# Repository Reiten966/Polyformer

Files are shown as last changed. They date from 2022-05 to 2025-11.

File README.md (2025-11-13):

# Polyformer
## To Reshape, Recreate, Reproduce.

As of late 2025, Polyformer is *no longer supported* due to a shift of focus in my life. Thanks for the amazing support of the community over the past 3 years. You could follow my future work at @reiten966

Polyformer is an open-source project that aims to recycle plastics into FDM filaments

Join the [Discord](https://discord.gg/jUtHzhddZZ) for Q&A. Please consider signing up for Patreon or Github sponsorship, link is on the right.

Note: The EBB42 V1.2.1 in the kit is no longer conpatible with the old firmware, please source EBB42 V1.2/V1.1 or help updating the firmware to support the new board.

The part kit is available at [Triangle Lab-Global](https://s.click.aliexpress.com/e/_DFp1dtz) and [DFH-US](https://dfh.fm/collections/new-products/products/polyformer-kit-by-reiten966).

Make sure your printer can print over 260C and is not PTFE lined.

Working on this project will expose you to HIGH VOLTAGE COMPONENTS and moderate amount of VOC. Please ask for help from a maker or electrician with the electronics assembly. The project owner is not responsible for any damage and loss to the end users.

Hero_34

Opening_Animation

[Project Page](http://www.reiten.design/polyformer)

[OSHWA US002136](https://certification.oshwa.org/us002136.html)

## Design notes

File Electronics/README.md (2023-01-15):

# Firmware Setup

If you bought the PF kit or plan to use EBB42 and Alexware, please refer to the EBB42 + Alexware folder.

If you plan to use klipper, please refer to the klipper folder.

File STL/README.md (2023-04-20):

# Print Guide

- The parts are DESIGNED to be manufactured with FDM technology with the proper tolerance stack in mind.

- Material Usage as of (9/21/2022): 1255g (2000g with panels) Main color and 400g accent color (1.25g/mm3 density). (We are constantly working on reducing the usage)

- Before you print anything, please print the [**PolyCube**](https://github.com/Reiten966/Polyformer/blob/main/STL/PolyTools) under the Tools folder and post your result in #print_help. The cube is a test for evaluating printer's performance and accuracy, we will help you intepret the result and suggest ways you can improve the quality.

- Use [**PolyTray**](https://github.com/Reiten966/Polyformer/blob/main/STL/PolyTools/PolyTray.STL) to organize your bolts and screws while building the Polyformer.

- Always dry your filament before printing mechanical parts, especially PETG. The blobs and strings cause by wet filaments can cause binding and malfunctioning the gearbox.

- The parts should be printed with at least **4 perimeters, 6 top and bottom layers**, set the seam type to "aligned" in Superslicer, or set to "sharpest corner" and "smart hiding" in Cura, **20% infill and 0.2mm layer height**. Cubic or gyro infill are usually pretty good. If you are using clear filament, Grid and honeycomb infill looks the nicest. You can also do concentric fill for your top and bottom layers which will look very nice.

- If you run into fitment issues and your printer has already been calibrated, try changing the "horizontal expansion" to -0.05 and increase if needed.

- Please also adjust the expansion rate in the slicer, you can do so by scaling the model only in XY direction by percentage, ABS has about ~0.6% shrinkage, PETG has about ~0.15%, I am not too sure about PLA (it has a lesser tendency to shrink than PETG so probably negligible) but you can do a test by printing a long bar across the plate and measure the dimension to calculate the shrinkage.

- In regards to the temperature for heatset inserts, PLA is around 225 °C, PETG is 245 °C, and ABS is 265 °C.

- All the functional parts can be printed on a 200mm x 200mm build plate. The panels can be printed on a 220mm x 200mm plate.

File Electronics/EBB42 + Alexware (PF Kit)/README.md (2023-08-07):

# Firmware for the PolyFormer stand alone pulling system
---

## Wiring Diagram
### EBB42
Wiring_Diagram_EBB42

### EBB36
Wiring_Diagram_EBB36

* [Wiring Guide In-Progress](https://discord.com/channels/969539629176991764/1062541608559579187)
* [Firmware deployment guide](firmware_deployment_guide.md)

Permission is hereby granted, free of charge, to any person obtaining a copy of this software and associated documentation files (the "Software"), to deal in the Software without restriction, including without limitation the rights to use, copy, modify, merge, publish, distribute, sublicense, and/or sell copies of the Software, and to permit persons to whom the Software is furnished to do so, subject to the following conditions:

The above copyright notice and this permission notice shall be included in all copies or substantial portions of the Software.

THE SOFTWARE IS PROVIDED "AS IS", WITHOUT WARRANTY OF ANY KIND, EXPRESS OR IMPLIED, INCLUDING BUT NOT LIMITED TO THE WARRANTIES OF MERCHANTABILITY, FITNESS FOR A PARTICULAR PURPOSE AND NONINFRINGEMENT. IN NO EVENT SHALL THE AUTHORS OR COPYRIGHT HOLDERS BE LIABLE FOR ANY CLAIM, DAMAGES OR OTHER LIABILITY, WHETHER IN AN ACTION OF CONTRACT, TORT OR OTHERWISE, ARISING FROM, OUT OF OR IN CONNECTION WITH THE SOFTWARE OR THE USE OR OTHER DEALINGS IN THE SOFTWARE.

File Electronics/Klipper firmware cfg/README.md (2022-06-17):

printer.cfg is for option 1

polyformer.cfg is for option 2

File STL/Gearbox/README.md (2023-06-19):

60% more torque at 2/3 the efficiency of the original!

Print two of each of the planet gears. When assembling, the planet gears should be evenly spaced around the ring gear (ie 90 degrees apart) and matching planets should be opposite each other. The faces with the squares/circles should be facing up (ie away from the stepper motor).

Print in PLA/PLA+ using the recommended PF print settings. I haven't tested this design with other materials but I'd avoid PETG as it flexes too much and will likely cause binding. If you print it out of something other than PLA/PLA+ I'd be interested to know how you go!

Tolerances are mostly baked into the design.

Heat set inserts go into the 4 holes in the output gear and these line up with the holes in the spool holder.

Link to Onshape document: https://cad.onshape.com/documents/80025b16f3dc0090e209a16d/w/86596204eff784e693332d0d/e/ddea801f1fdb4b026ff6d2b4 There's a bunch of other nonsense in there as well. I don't guarantee that any of it will work.





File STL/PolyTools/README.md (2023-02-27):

# PolyTools

## PolyCube

Testing printer accuracy and overhang capability

Items that are tested:

-45 degree overhangs

-Print-in-place tolerance

-Flow percentage

-Compliant 12mm tube fastener

-Bearing fitment

-Vertical 12mm tube fitment

Post your result in #print_help

How to read Polycube

## PolyPlane

Used for sharpening bearings, achieving a better cutting performance

-4x M3x8mm

-6x 623 bearings

## PolyTray

Identifying screws size and storing screws

-19x 6x3mm Neodymium magnets

## PolyClip

Constructing bigger boxes using smaller boxes for bottle collection

-No assembly, print-in-place

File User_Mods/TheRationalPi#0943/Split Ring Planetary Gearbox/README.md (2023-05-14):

THIS IS NOW THE OFFICIAL GEARBOX AND PROBABLY WON'T BE UPDATED HERE, JUST GET IT FROM THE STL FOLDER

60% more torque at 2/3 the efficiency!

This is my 70:1 split ring planetary gearbox for the PolyFormer. It uses the existing gearbox as a base and should be a drop-in replacement. This uses the existing gearbox cap, grab that from the main STL/Gearbox folder. Print two of each of the planet gears. When assembling, the planet gears should be evenly spaced around the ring gear (ie 90 degrees apart) and matching planets should be opposite each other. The faces with the squares/circles should be facing up (ie away from the stepper motor).

Print in PLA/PLA+ using the recommended PF print settings. I haven't tested this design with other materials but I'd avoid PETG as it flexes too much and will likely cause binding. If you print it out of something other than PLA/PLA+ I'd be interested to know how you go!

Tolerances are mostly baked into the design.

Heat set inserts go into the 4 holes in the output gear and these line up with the holes in the spool holder. These are the same M3 x 5 x 4 heat set inserts as used in the PF BOM. 

Link to Onshape document: https://cad.onshape.com/documents/80025b16f3dc0090e209a16d/w/86596204eff784e693332d0d/e/ddea801f1fdb4b026ff6d2b4

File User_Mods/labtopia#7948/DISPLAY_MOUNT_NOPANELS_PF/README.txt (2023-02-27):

labtopia#7948
2_19_23
LABTOPIAS_IMPERFECT_DFHKIT_DISPLAY_MOUNT

I made this quickly to mount the DFH kit display for my polyformer with no panels.  It slides into the holes of the frame.  I drilled pilot holes into the screw mount points and used some short small screws.
.stl only

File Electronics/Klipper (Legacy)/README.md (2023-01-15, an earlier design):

# Firmware Setup

### Its a good idea to flash the firmware for Pi and MCU **BEFORE** you follow the part 4 video to install them on the machine.

## Option2: (Klipper: Voron printer + Compatible MCU)

- Plug the SKR pico to the pi via USB on your printer, and add the polyformer.cfg into your printer's config as below
  
- And then include the polyformer.cfg in your main printer.cfg as below
  

- Follow the Klipper installation on SKR Pico above.

## Option3: (Marlin: Compatible MCU + Screen)

Guide in progress, please ask in the discord.

# Wiring Guide

- UART setup
  Polyformer-Electronics-RPi-SKR-Pico1 0

- USB setup
  

# PID Calibration Procedure

This procedure is for calibrating the heater cartridge.

**Reference documentation**

- [Bigtree SKR Pico v1.0 + RPi setup](https://3dwork.io/en/skr-pico-analysis-and-complete-guide-of-this-great-little-controller)
- [Basic Klipper Configuration](https://3dwork.io/en/skr-pico-analysis-and-complete-guide-of-this-great-little-controller/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)
- [Mainsail](https://docs.mainsail.xyz/)
- [Installing MainsailOS](https://docs.mainsail.xyz/setup/mainsail-os)
- [Klipper3D](https://www.klipper3d.org)

## Pre-reqs

The following instructions assume the following:

- Your hardware setup matches the diagram the provided diagram `Polyformer-Electronics-RPi-SKR-Pico1.0-Working.png`
- Your RaspberryPi has been configured for UART integration. If not, follow this guide [Basic Klipper Configuration](https://3dwork.io/en/skr-pico-analysis-and-complete-guide-of-this-great-little-controller/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)
- _MainsailOS_ (_Mainsail_, _klipper_, and _Moonracker_) are install and running on the _RaspberryPi_
- Your _SKR Pico v1.0_ control board has been flashed with the latest stable firmware and has `UART` support. The name of your firware image should be `klipper-UART0.uf2`
- You are using the attached klipper config `printer.cfg`
- _Mainsail_ web UI is acceesible and there are no errors reported by klipper on the _Mainsail_ dashboard.

**IMPORTANT:** ALL pre-qeqs MUST be satified in order to proceed.

## Instructions

1. Open a web brower and go to the Mainsail website that is running on your RapsberryPi
2. Open the _G-Code console_ on the Mainsail web UI
3. Run the following g-code command to calibrate. This will take about 5 minutes to complete:

```
PID_CALIBRATE HEATER=extruder TARGET=210
```

4. Run this command to save the PID calibration coeffs to the 'printer.cfg' file

```
SAVE_CONFIG
```

5. Click the _Save and Restart_ button to reconfigure _Klipper_
6. Verify temperature stabiity

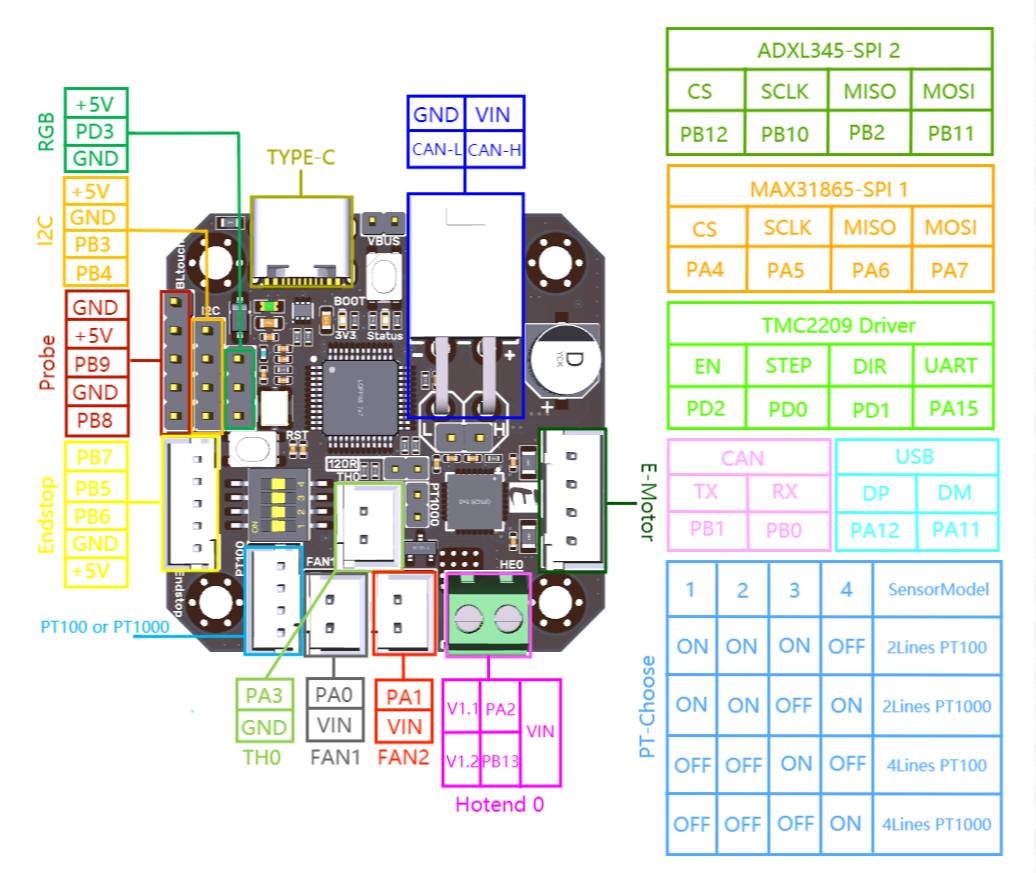
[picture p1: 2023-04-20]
Electronics/EBB42 + Alexware (PF Kit)/images/EBB42 CAN V1.1&V1.2-PIN.png

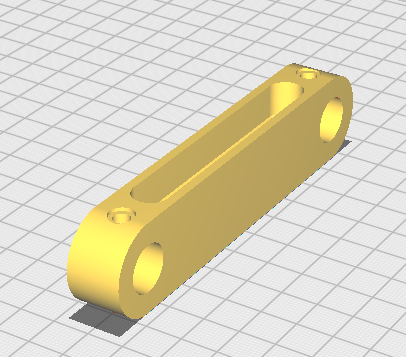
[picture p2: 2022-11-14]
STL/Carriages/Images/Electronics_Bracket_4x.png

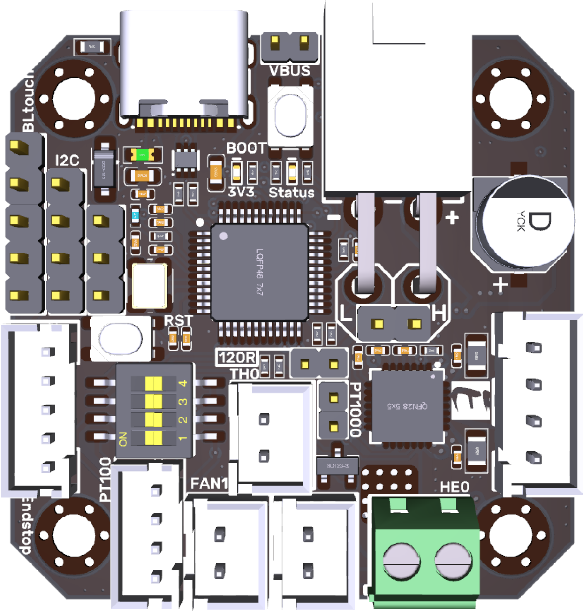
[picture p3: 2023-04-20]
Electronics/EBB42 + Alexware (PF Kit)/images/EBB42 CAN V1.1&V1.2.png

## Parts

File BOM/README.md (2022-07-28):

[BOM](https://docs.google.com/spreadsheets/d/1AnlkvCJu0GFPeh3ZkoAeYPVGYUqE0VFktIv_mGqOwsU/edit#gid=570414797)

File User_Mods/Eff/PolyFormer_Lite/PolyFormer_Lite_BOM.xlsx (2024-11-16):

Category | Part | Qty | Price/Un (BRL) | Total Price(BRL) | Price (direct USD conversion)
Electronics | Knock-off E3D V6 HotEnd Assembly | 1 | R$99.00 | R$99.00 | $16.89
 | W1209k Thermostat Board | 1 | R$39.00 | R$39.00 | $6.66
 | PWM controller | 1 | R$40.00 | R$40.00 | $6.83
 | Jgy370 12v Dc Motor | 1 | R$90.00 | R$90.00 | $15.36
 | 60x10 PC fan | 2 | R$29.00 | R$58.00 | $9.90
 | Dc 12v 10a psu | 1 | R$38.00 | R$38.00 | $6.48
 | Female p4 dc jack | 1 | R$15.00 | R$15.00 | $2.56
 | Wiring | 1 | R$25.00 | R$25.00 | $4.27
Fasteners | M3 nut | 50 | R$0.07 | R$3.50 | $0.60
 | M3x6 | 50 | R$0.07 | R$3.50 | $0.60
 | M3x12 | 50 | R$0.07 | R$3.50 | $0.60
 | M3x20 *Stainless steel* | 4 | R$0.07 | R$0.28 | $0.05
Misc | 608 bearings | 4 | R$10.00 | R$40.00 | $6.83
 | PTFE Lubricant | 1 | R$39.00 | R$39.00 | $6.66
 | 1.6mm HSS DrillBit | 1 | R$25.00 | R$25.00 | $4.27
 |  | 1 | R$0.00 | R$0.00 | $0.00
 |  | 1 | R$0.00 | R$0.00 | $0.00
 | TOTAL |  |  | R$518.78 | $88.53
Part | Weight(g) |  | Print Time
Chassis | 567g |  | 0.04027777778
Dc Motor Hub | 50g |  | 0.04027777778
Ribbon Mount | 100g |  | 0.04027777778
Ribbon Spool | 25g |  | 0.04027777778
Spool | 140g |  | 0.04027777778
Spool Top | 98g |  | 0.04027777778
Guidler | 90g |  | 0.04027777778
Total Weight | 1070g
Total Print Time | 0.2819444444

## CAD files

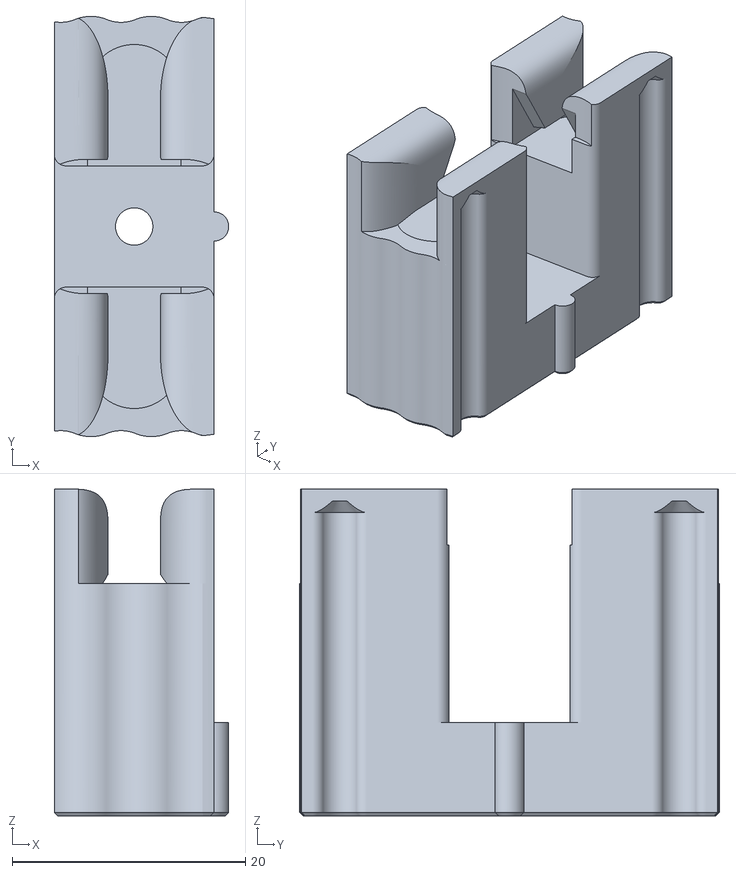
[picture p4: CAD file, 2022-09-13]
STL/Bottle_Cutter (no supports)/Sliding_Gauge.stl
15.0 x 36.0 x 28.0

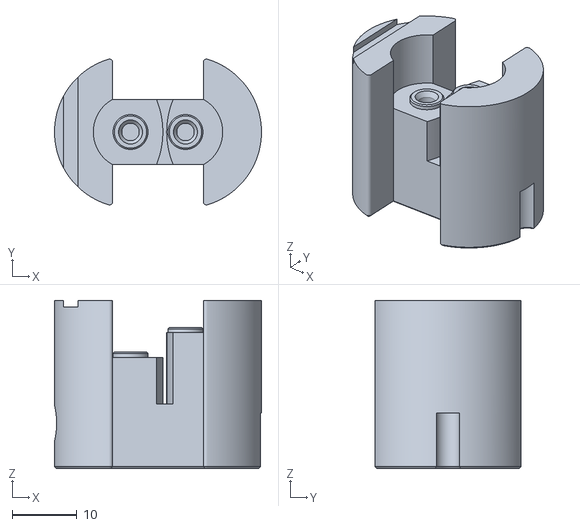
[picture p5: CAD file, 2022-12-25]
STL/Bottle_Cutter/Cutter.stl
32.0 x 22.5 x 26.0

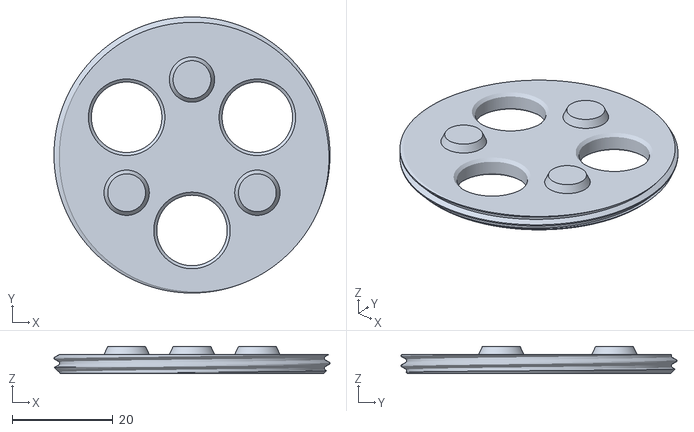
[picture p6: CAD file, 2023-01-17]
STL/Carriages/Ribbon_Cartridge_Cap_2x.stl
54.9 x 54.9 x 5.40

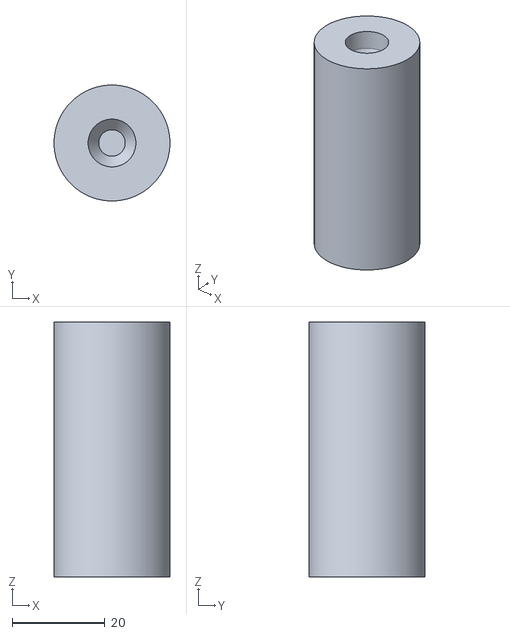
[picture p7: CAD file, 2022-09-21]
STL/Carriages_(no supports)/Filament_Guidler_Spindle.stl
25.0 x 25.0 x 55.0

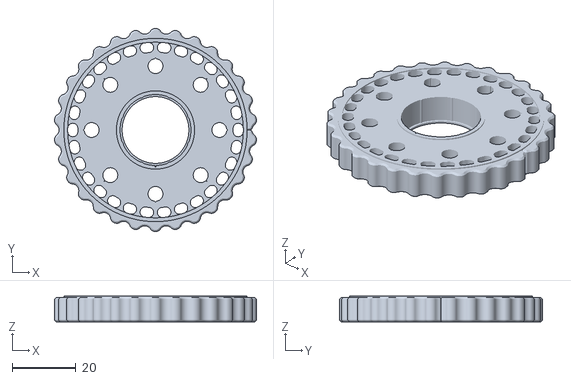
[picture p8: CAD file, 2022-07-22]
STL/Gearbox (no supports)/Gear_Box_Ring_Gear.stl
63.3 x 63.6 x 8.00

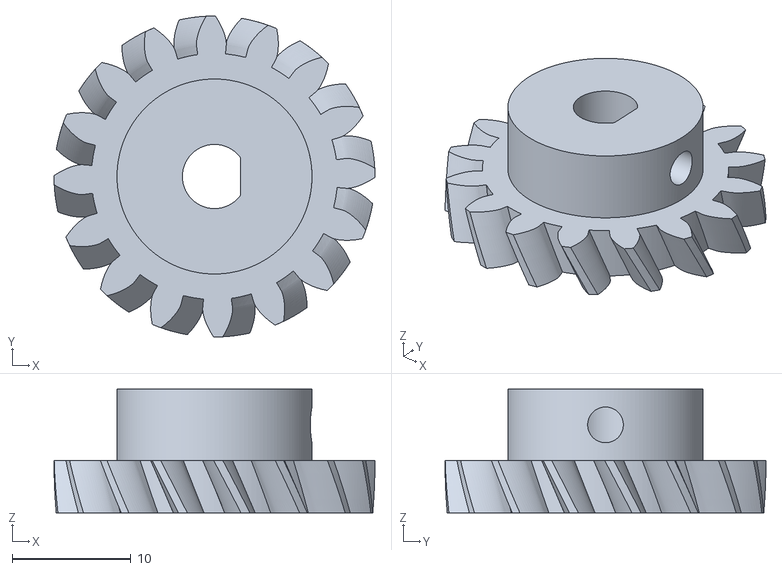
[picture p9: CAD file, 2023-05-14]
STL/Gearbox/Input Sun 16T.stl
27.0 x 27.0 x 10.4

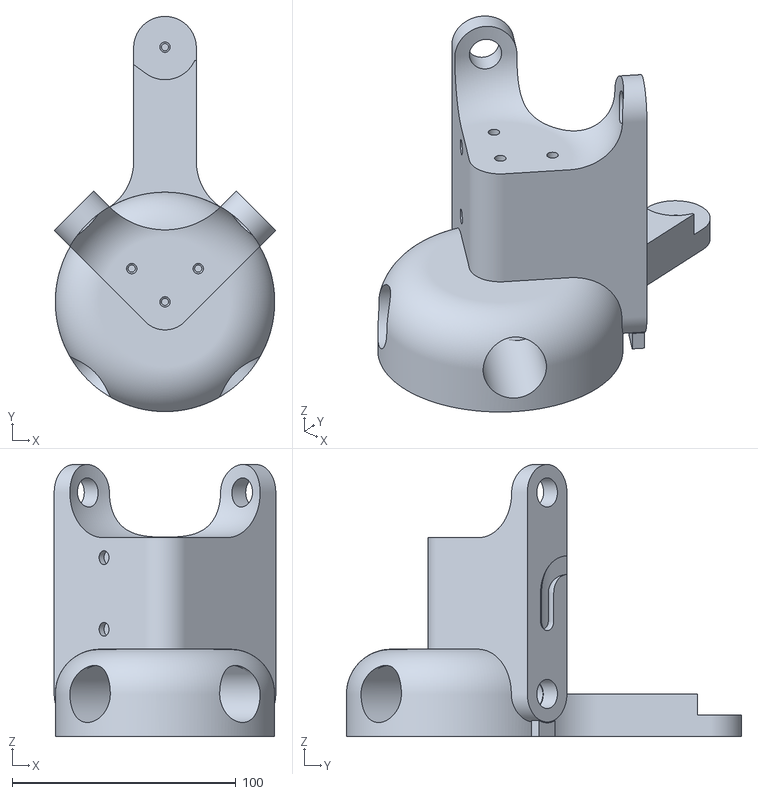
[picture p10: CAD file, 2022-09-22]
STL/Main_Body (no supports unless noted)/Left_Lower_Arm_(Built-in Supports).stl
99.0 x 176.5 x 121.5

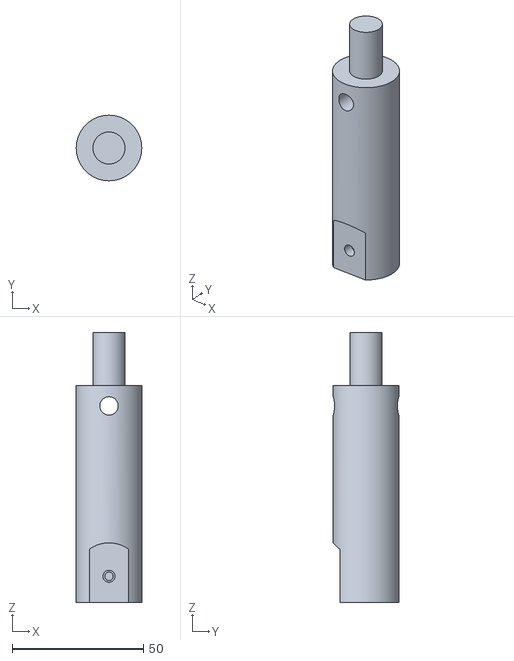
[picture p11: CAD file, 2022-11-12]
STL/Main_Body/Panel_Stabilizer_x2.stl
25.0 x 25.0 x 103.0

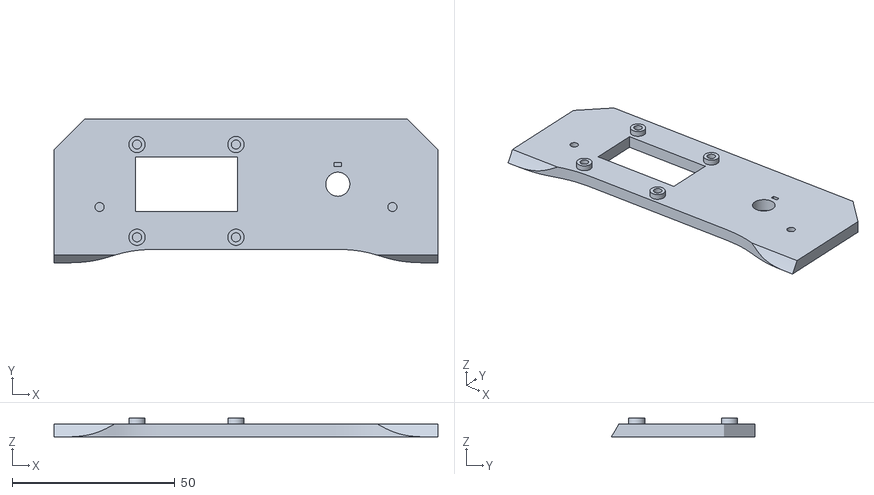
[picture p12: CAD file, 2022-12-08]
STL/Panels (Optional)/Screen_Mount.stl
118.0 x 44.2 x 5.80

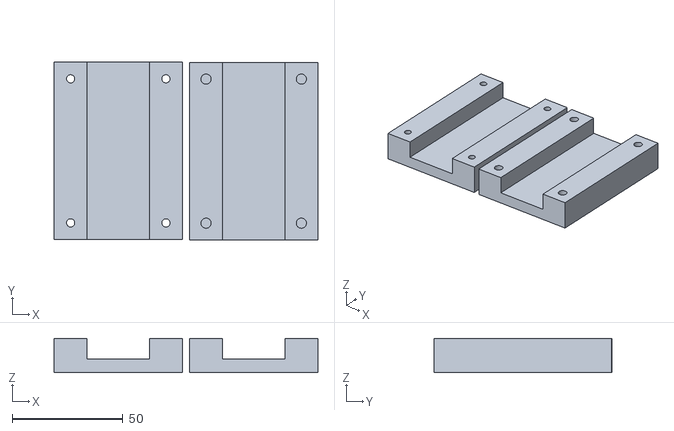
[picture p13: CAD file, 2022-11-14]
STL/PolyTools/Left_Arm_Reinforcement_Block_For_Shipping.STL
119.1 x 80.1 x 15.5

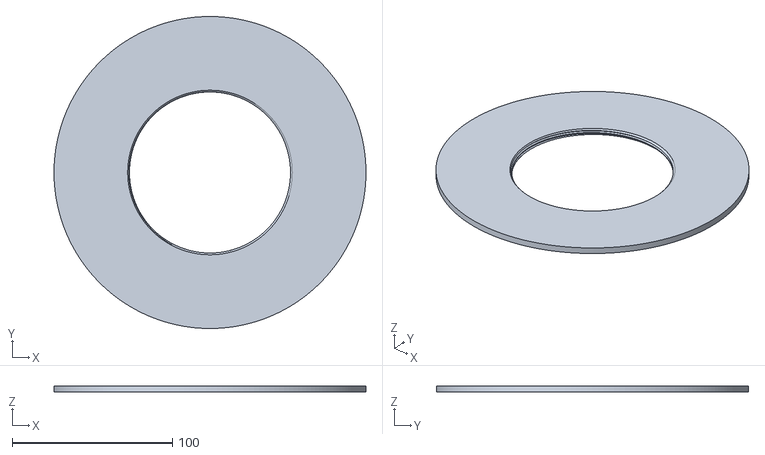
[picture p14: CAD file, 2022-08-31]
STL/Spool (no supports)/[Accent Color] Spool_Shield_Left.stl
195.0 x 195.0 x 4.00

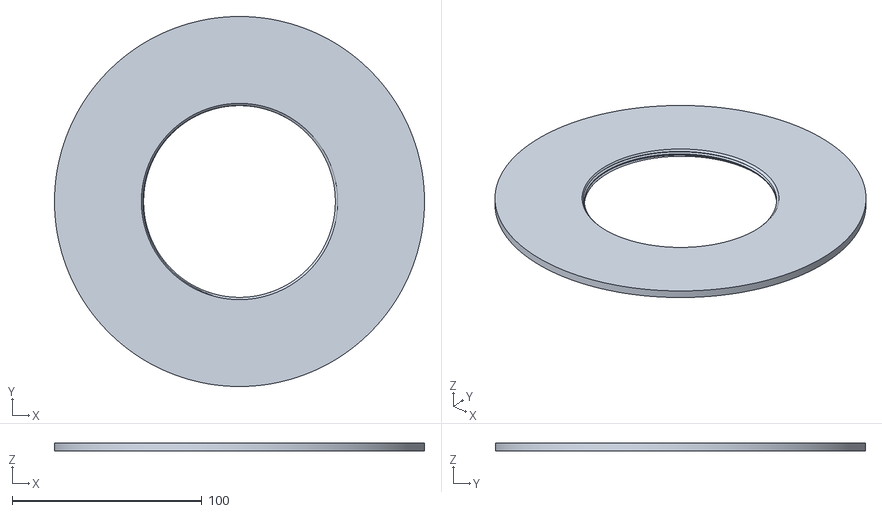
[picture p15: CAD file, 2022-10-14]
STL/Spool/[Accent Color] Spool_Shield_Left.stl
195.0 x 195.0 x 4.00

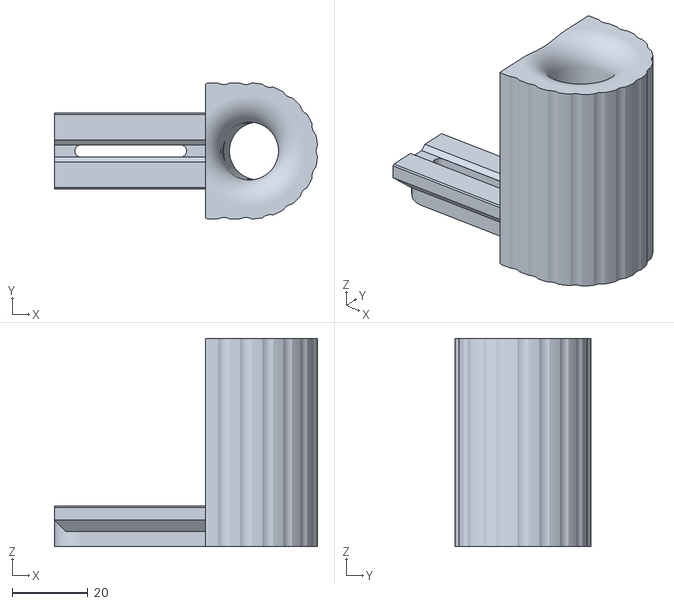
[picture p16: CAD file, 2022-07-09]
User_Mods/Alextrical#1192/608 Polycutter Lite/15MM Pipe/Bottle_Holder_608_15mmPipe.stl
69.6 x 36.0 x 55.2

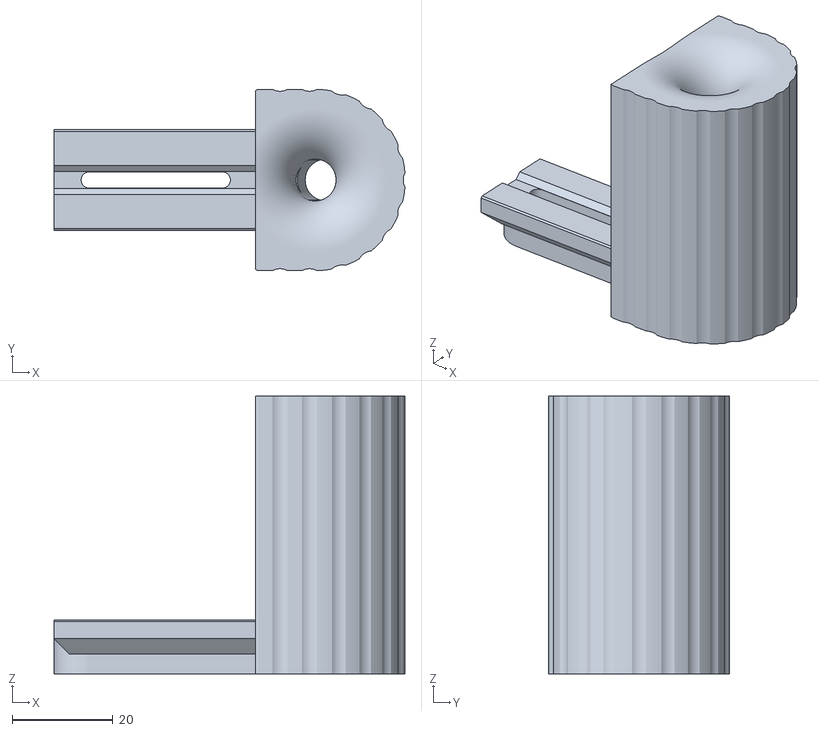
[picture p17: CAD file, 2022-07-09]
User_Mods/Alextrical#1192/608 Polycutter Lite/8MM Pipe/8mm Bottle Guide.stl
69.6 x 36.0 x 55.2

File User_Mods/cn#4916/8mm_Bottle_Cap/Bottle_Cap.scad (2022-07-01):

$fn = 72;

import("./../../STL/Bottle_Cutter (no supports)/Bottle_Cap.STL");

difference() {
    cylinder(d=12,12.5);
    cylinder(d=8.2,16);
}

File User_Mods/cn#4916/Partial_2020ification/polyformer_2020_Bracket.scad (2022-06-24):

$fn = 72;

difference() {
union() {

import("../../STL/Main_Body (no supports unless noted)/Frame_Bracket_(Needs Supports).stl");

rotate([45,0,0]) {
translate([0,45,5])
cube([10+20,70-15,20], true);
    
*translate([5+20,45,5])
%cube([20,100,20], true);

*translate([-25,45,5])
%cube([20,100,20], true);
    
translate([-45,62.225,5])
    rotate([90,0,0])
    difference() {
        cylinder(d=13,8.5);
        translate([0,0,-1])
            cylinder(d=5.2,11);
}

translate([45,62.225,5])
    rotate([90,0,0])
    difference() {
        cylinder(d=13,8.5);
        translate([0,0,-1])
            cylinder(d=5.2,11);
}
}

}

rotate([45,0,0]) {
translate([5+20,67.5,5])
#cube(20.25, true);

translate([-25,67.5,5])
#cube(20.25, true);
}

}

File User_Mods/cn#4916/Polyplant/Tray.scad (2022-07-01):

$fn=144;

difference() {
    scale([1.5,1.5,1])
import("/path/to/Polyformer/[Accent Color] Spool_Body.stl");

translate([0,0,-0.1])
    # cylinder(d=160,45.1);
}

translate([0,0,44])
    cylinder(d=155,3);

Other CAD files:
User_Mods/Alextrical#1192/608 Polycutter Lite/CAD/Polycutter Lite 608ZZ_6_17_2022.step
User_Mods/Alextrical#1192/608 Polycutter Lite/Sliding_Gauge_608.stl
User_Mods/Alextrical#1192/608 Spool shaft knob/608 Spool Shaft Knob Cap.stl
User_Mods/Alextrical#1192/Boilerplate/PF007 Dréço Plate.stl
User_Mods/cn#4916/Spool_Adaptor/spool_adaptor.scad
STL/Bottle_Cutter (no supports)/Body.stl
STL/Bottle_Cutter (no supports)/Bottle_Cap.STL
STL/Bottle_Cutter (no supports)/Bottle_Holder.stl
STL/Bottle_Cutter (no supports)/Cutter.stl
STL/Bottle_Cutter/Body.stl
STL/Bottle_Cutter/Bottle_Cap.STL
STL/Bottle_Cutter/Bottle_Cap_Tensioner.STL
STL/Bottle_Cutter/Bottle_Holder.stl
STL/Bottle_Cutter/Sliding_Gauge.stl
STL/Carriages/DC_Plug_Adapter_(TriangleLab_Kit).stl
STL/Carriages/DFH_Inlet.stl
STL/Carriages/Electronics_Bracket_4x.stl
STL/Carriages/Filament_Guidler_(built_in_supports).stl
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

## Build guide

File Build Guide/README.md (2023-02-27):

# Video Guides

[Polyformer assembly video part 1](https://www.youtube.com/watch?v=gqaRRzHKmp0)

[Polyformer assembly video part 2 & 3](https://youtu.be/NvOG5K5bJ6M)

[Polyformer assembly video part 4](https://youtu.be/LeM5dLHGVpM)

[Heatset inserts tutorial](https://youtu.be/gEWWZhYNxxQ)

[Polycutter Lite assembly video](https://www.youtube.com/watch?v=EgzWEFJ99so)

[Polyformer operation video](https://www.youtube.com/watch?v=f05WWMm3e6w&t=1s)

Please refer to the Assembly Guides made by @lhong820#0249 for assembly.

Make sure you run Polyformer in a well ventilated area.

# rPET print settings

260-280C Nozzle temp

70-80C Bed Temp

120-130% flow (higher due to the hollow bore nature of the filament, needs to be calibrated)

20-40% fan

60mm/s minimum print speed

DRY YOUR PET BEFORE PRINT FOR BEST RESULT

Retraction and other settings is dependent on your printer, But in general PET behaves similarly to PETG.
One thing special about PET is that it requires you to print moderately fast, in order to prevent hot filament from staying too long inside the heatbreak which will lead to the filament crystalizing and jam inside the heatbreak. If you see the printed part turning white, that is also a sign of the filament staying hot for too long after exiting the nozzle, which you should fix by increasing the fan speed.

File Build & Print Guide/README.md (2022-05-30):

The parts should be printed with at least 4 perimeters, 6 top and bottom layers, 40% infill and 0.2mm layer height. Cubic or gyro infill are usually pretty good. If you are using clear filament, Grid and honeycomb infill looks the nicest. You can also do concentric fill for your top and bottom layers which will look very nice.

Please also adjust the expansion rate in the slicer, you can do so by scaling the model only in XY direction by percentage, ABS has about ~0.6% shrinkage, PETG has about ~0.15%, I am not too sure about PLA (it has a lesser tendency to shrink than PETG so probably negligible) but you can do a test by printing a long bar across the plate and measure the dimension to calculate the shrinkage.

The Part "Melt_Zone" is recommended to print with a more heat resistant material such as PETG or ABS. PLA is not tested.

Polyformer assembly video part 1

https://www.youtube.com/watch?v=gqaRRzHKmp0

Polyformer assembly video part 2

https://youtu.be/Hwx7r2c6wwA

Bottle cutter assembly video

https://www.youtube.com/watch?v=mIvZ6ZM0HBI

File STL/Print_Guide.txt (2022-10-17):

# Print Guide

- Material Usage as of (9/21/2022): 2000g Main color and 500g accent color (1.25g/mm3 density). (We are constantly working on reducing the usage)

- Before you print anything, please print the **PolyCube** under the Tools folder and post your result in #print_help. The cube is a test for evaluating printer's performance and accuracy, we will help you intepret the result and suggest ways you can improve the quality.

- It is recommended to use Superslicer or Cura which has individual control for overhangs. Prusaslicer is not recommended. You can also slow down the perimeter speed and increase fan speed if your slicer doesn't support lowering overhang speed.

- Always dry your filament before printing mechanical parts, especially PETG. The blobs and strings cause by wet filaments can cause binding and malfunctioning the gearbox.

- The parts should be printed with at least 4 perimeters, 6 top and bottom layers, set the seam type to "aligned" in Superslicer, or set to "sharpest corner" and "smart hiding" in Cura, 20% infill and 0.2mm layer height. Adaptive Cubic/Cubic or gyro infill are usually pretty good. If you are using clear filament, Grid and honeycomb infill looks the nicest. You can also do concentric fill for your top and bottom layers which will look very nice.

- Please also adjust the expansion rate in the slicer, you can do so by scaling the model only in XY direction by percentage, ABS has about ~0.6% shrinkage, PETG has about ~0.15%, I am not too sure about PLA (it has a lesser tendency to shrink than PETG so probably negligible) but you can do a test by printing a long bar across the plate and measure the dimension to calculate the shrinkage.

- In regards to the temperature for heatset inserts, PLA is around 225 °C, PETG is 245 °C, and ABS is 265 °C.

- All the functional parts can be printed on a 200mm x 200m build plate. The panels can be printed on a 220mm x 200mm plate.

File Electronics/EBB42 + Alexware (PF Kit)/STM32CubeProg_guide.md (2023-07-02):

# STM32CubeProg
---

# Windows | Mac | Linux

The easiest way by far to program the board is to download STM32CubeProg. It's a graphical programmer, and does not require Zadig or special command line invocation. Download the earliest version available from their website after 2.1.0 (e.g. 2.5.0 is fine), otherwise, the writing process will not complete successfully.

You'll need to make a ST.com account is the only downside.

[Download STM32CubeProg(please download 2.50 version)](https://www.st.com/en/development-tools/stm32cubeprog.html)

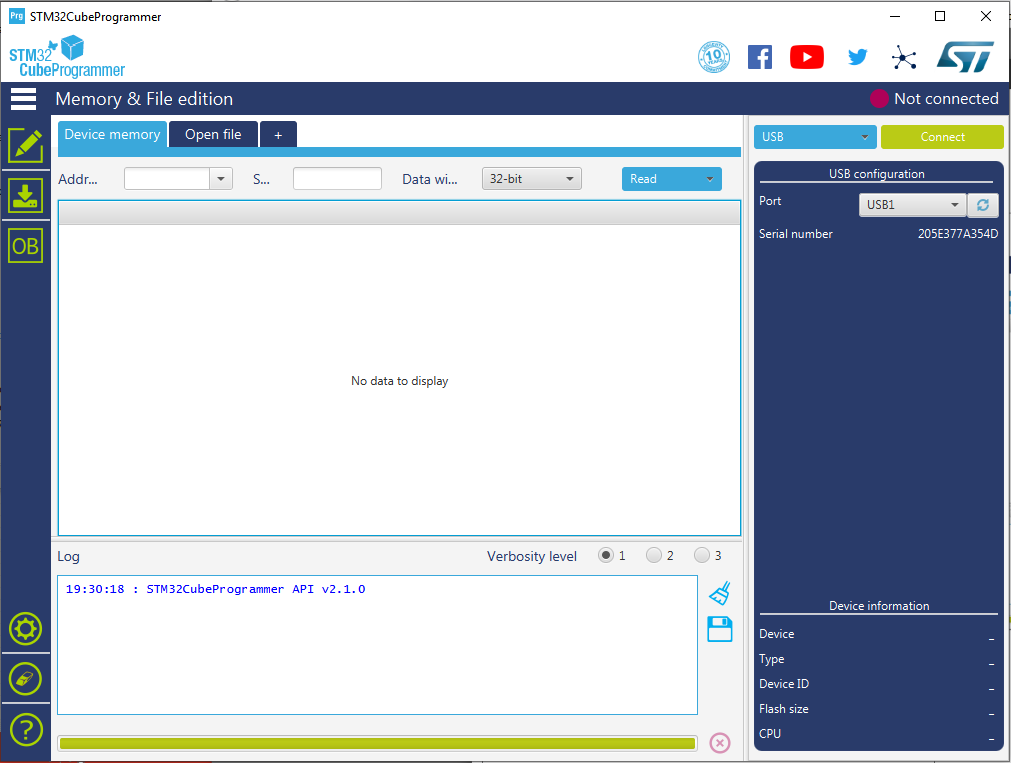
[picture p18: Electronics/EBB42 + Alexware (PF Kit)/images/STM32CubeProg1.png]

When you start it up, it'll look like this.

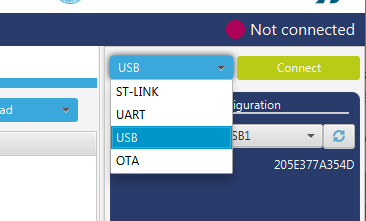
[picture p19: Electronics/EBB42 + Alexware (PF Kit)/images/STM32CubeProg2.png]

In the top right, below the Not Connected message, find the dropdown to the left of the Connect button
Select "USB"

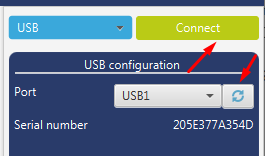
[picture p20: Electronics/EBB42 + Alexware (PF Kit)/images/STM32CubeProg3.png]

If the device is plugged in and the bootloader is running, it will show up under the USB configuration pane. If not, enter bootloader mode by holding BOOT and pressing RST (you shoudl see a blue LED on the board). Click the refresh button.
Once it appears as a valid Port, click Connect

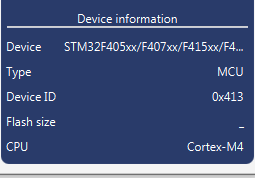
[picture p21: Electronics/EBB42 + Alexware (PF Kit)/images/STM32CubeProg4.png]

You should see the Device info pane in the bottom right is updated with info about what chip was found!

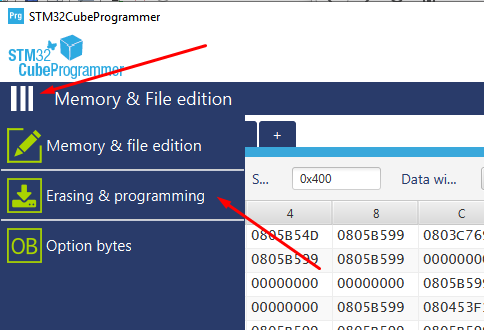
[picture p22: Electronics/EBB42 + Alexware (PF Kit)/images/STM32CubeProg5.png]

Click the 3-lines below the STM32 logo in the top left, to expand the menu.
Then click Erasing & Programming

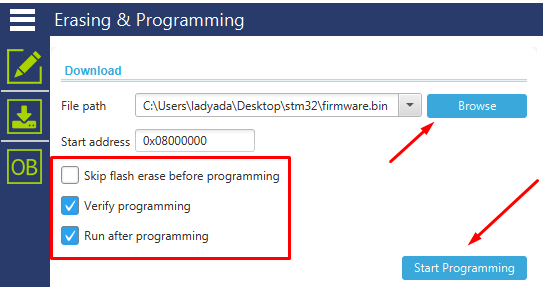
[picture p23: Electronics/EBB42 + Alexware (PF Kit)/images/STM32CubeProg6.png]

Click Browse to open the firmware files you want to program.
You can program .hex or .bin files.
Don't change the Start Address.
Make sure Verify Programming and Run after Programming are clicked, but Skip flash erase is not.
Then click Start Programming.

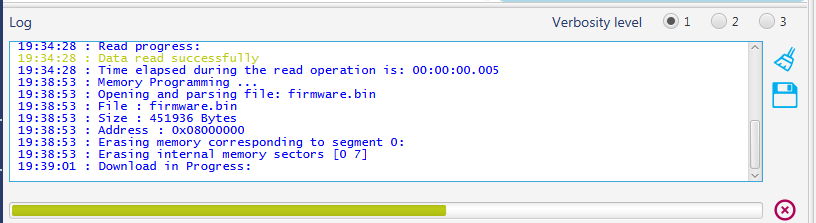
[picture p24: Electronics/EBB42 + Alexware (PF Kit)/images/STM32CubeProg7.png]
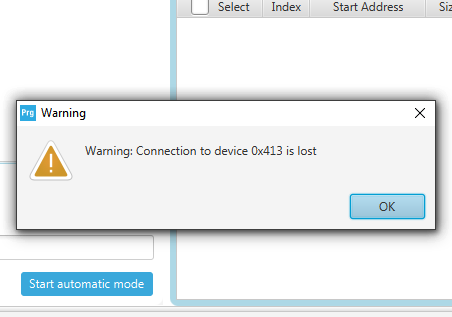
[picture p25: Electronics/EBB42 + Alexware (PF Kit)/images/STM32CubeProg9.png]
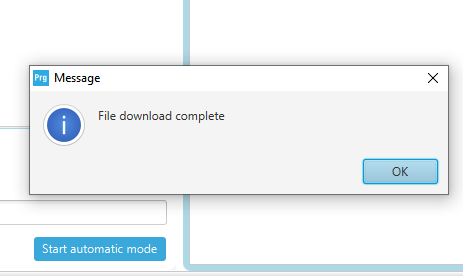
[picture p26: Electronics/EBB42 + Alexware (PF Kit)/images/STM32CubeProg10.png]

It will take a few seconds to erase and reprogram the chip.
It's normal to get a Warning Connection is lost alert.
Click away until you get the File download complete alert.

That's it! You can close STM32 CubeProg.

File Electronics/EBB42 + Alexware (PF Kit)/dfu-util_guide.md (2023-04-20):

# dfu-util
---

# Windows | Mac | Linux

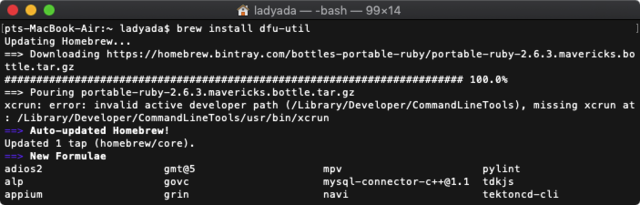
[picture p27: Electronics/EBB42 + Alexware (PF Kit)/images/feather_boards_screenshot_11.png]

For Mac users, install dfu-util with brew `brew install dfu-util`

For Linux users, 
Ubuntu/Debian: `sudo apt-get install dfu-util`
Fedora: `yum install dfu-util`

For windows users, [download here](https://sourceforge.net/projects/dfu-util/)

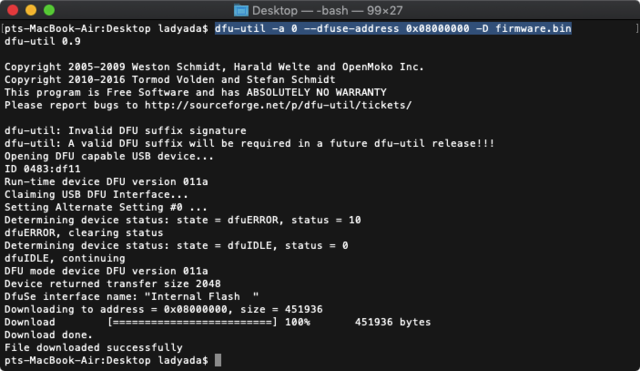
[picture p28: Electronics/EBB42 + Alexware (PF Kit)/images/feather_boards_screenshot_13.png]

Upload the firmware with the command:
`dfu-util -a 0 --dfuse-address 0x08000000 -D firmware.bin`
Don't change the address value, only the firmware filename!

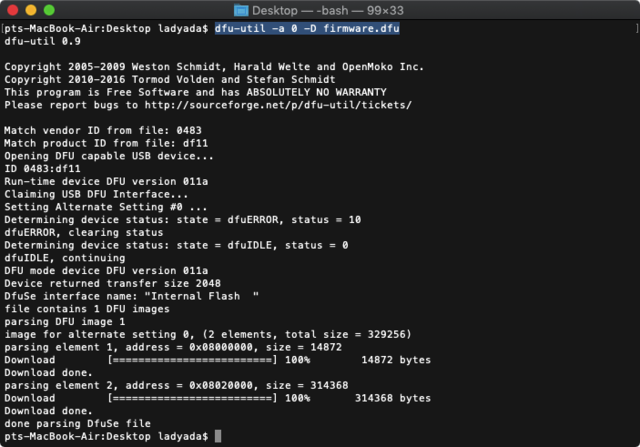
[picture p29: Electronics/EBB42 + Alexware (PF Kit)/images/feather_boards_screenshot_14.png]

Upon success, reset the board without the BOOT button and you will see after a few seconds the screen light up.

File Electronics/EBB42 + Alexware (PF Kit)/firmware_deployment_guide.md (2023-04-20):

# EBB42: Firmware Deployment Guide
---
## Preparing the board for firmware installation (Entering DFU mode)
The firmware files are located [here](https://github.com/Reiten966/Polyformer/tree/main/Electronics/EBB42%20%2B%20Alexware%20(PF%20Kit)/Firmware), the EBB42 has no firmware installed by default when shipped out. You can upload the firmware using STM32CubeProgrammer or dfu-util.

* Enable USB Power
    
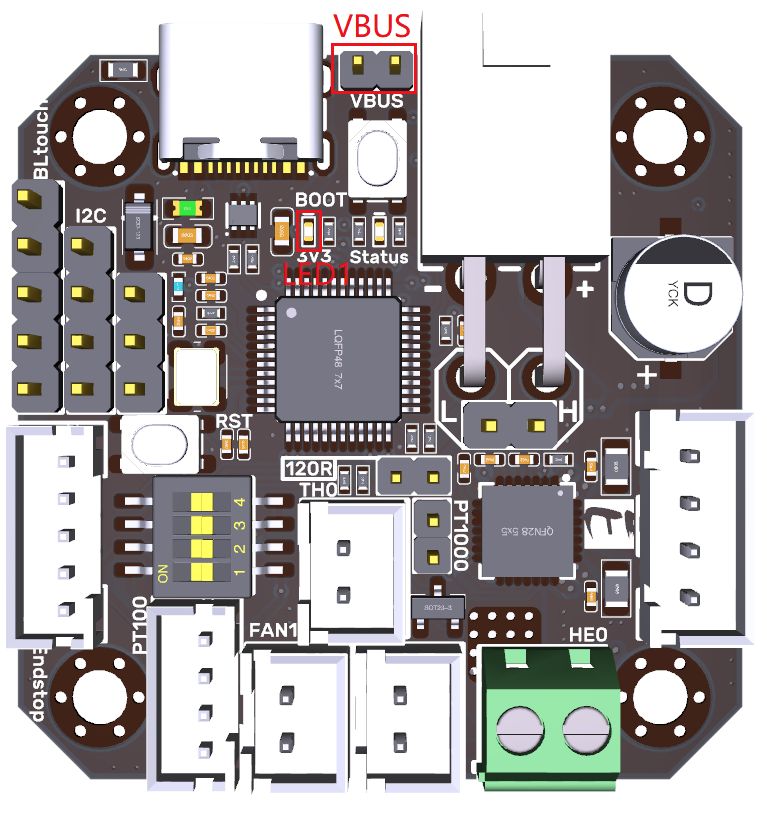
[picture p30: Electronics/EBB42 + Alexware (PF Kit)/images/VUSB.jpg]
    When connected via USB, the green LED should light up. If it doesnt light up, you need attach the jumper across VUSB.

* Enabling DFU bootloader mode 

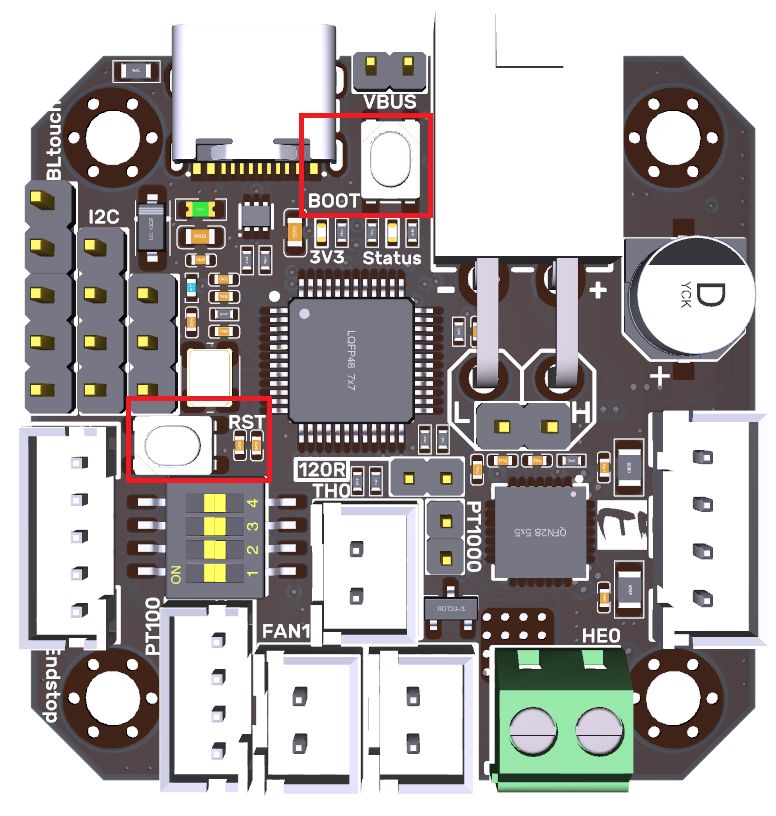
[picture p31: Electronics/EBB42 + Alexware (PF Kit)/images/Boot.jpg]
    Enabling the DFU bootloader is super easy. Simply hold down the BOOT button. Then press the RST button or power cycle while the board is connected to your computer USB port. The led will glow dull blue if you have done this correclty. If you get no LED's iluminated, make sure the jumper is conected across 'VBUS' After you've hit reset, you can release the BOOT button - it's only checked on powerup

* Check for USB Bootloader device
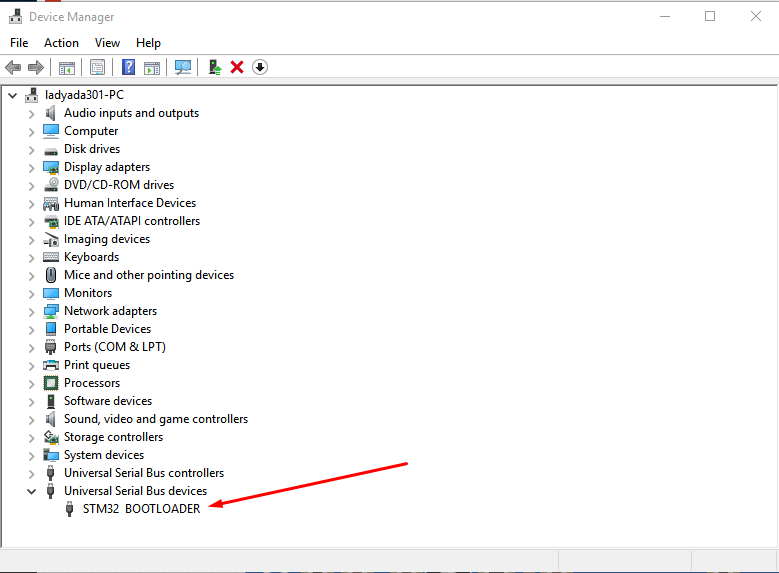
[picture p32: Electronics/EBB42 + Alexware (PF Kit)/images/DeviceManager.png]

In Windows, in "Device Manager", you will see the device show up as "STM32 BOOTLOADER" under Universal Serial Bus devices

In MacOS X. Visit the AppleMenu->About This Mac->System Report. Select USB and look for the item labeled "STM32 BOOTLOADER"
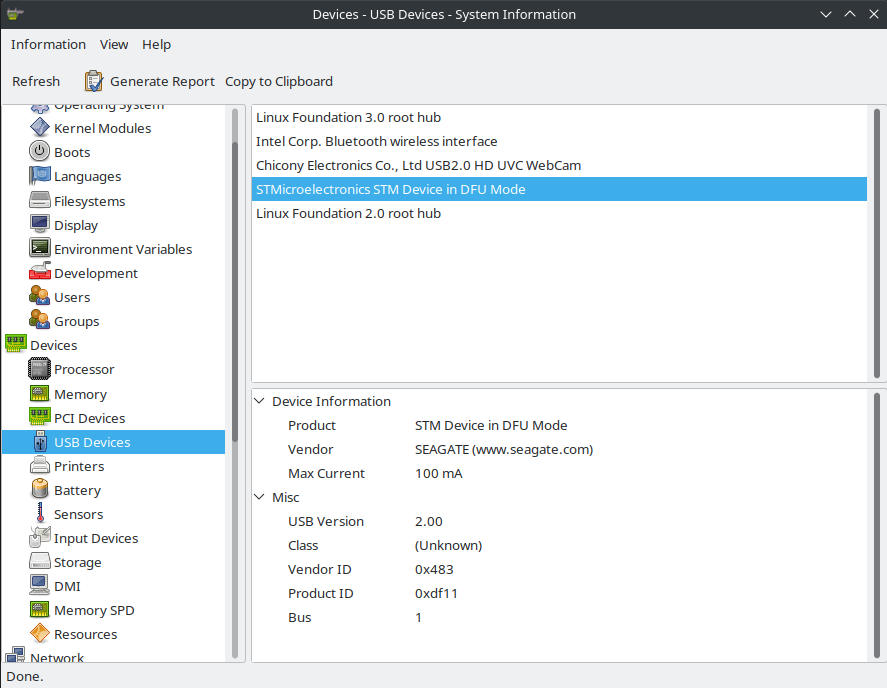
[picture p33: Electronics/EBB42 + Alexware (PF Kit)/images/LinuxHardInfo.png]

In Linux, use HardInfo `sudo apt install hardinfo`

## Installing the firmware
---
* [Using STM32CubeProg](STM32CubeProg_guide.md): The easiest way by far to program, is to download STM32CubeProg. It's a graphical programmer and does not require Zadig or special command line invocation.

    The only downside is you'll need to make an ST.com account. 
    
    This [video](https://youtu.be/_FELCN8CbWA?t=385) (watch 6:24-8:06) by Eddie shows you how to install any firmware on EBB42, you just need to load the PolyFormerFW_Vx.x.bin file instead.

* [Using dfu-util](dfu-util_guide.md): Command line tool for programming.

## References

<!-- * [EBB42 Introduction](EBB42_introduction.md) -->
<!-- * [Firmware Architecture Overview](firmware_architecture_overview.md) -->
<!-- * [System Firmware Change-log](system_firmware_changelog.md) -->
<!-- * [Windows Driver Installation Guide](windows_driver_installation_guide.md) -->
* [STM32CubeProg Installation Guide](STM32CubeProg_guide.md)
* [dfu-util Installation Guide](dfu-util_guide.md)
* [Polyformer Disord](https://discord.gg/JUNUWZkG)
* [Adafruit](https://learn.adafruit.com/adafruit-stm32f405-feather-express/dfu-bootloader-details)

## Resources

* [Firmware Binaries](https://github.com/Reiten966/Polyformer/tree/main/Electronics/EBB42%20%2B%20Alexware)

## License

Permission is hereby granted, free of charge, to any person obtaining a copy of this software and associated documentation files (the "Software"), to deal in the Software without restriction, including without limitation the rights to use, copy, modify, merge, publish, distribute, sublicense, and/or sell copies of the Software, and to permit persons to whom the Software is furnished to do so, subject to the following conditions:

The above copyright notice and this permission notice shall be included in all copies or substantial portions of the Software.

THE SOFTWARE IS PROVIDED "AS IS", WITHOUT WARRANTY OF ANY KIND, EXPRESS OR IMPLIED, INCLUDING BUT NOT LIMITED TO THE WARRANTIES OF MERCHANTABILITY, FITNESS FOR A PARTICULAR PURPOSE AND NONINFRINGEMENT. IN NO EVENT SHALL THE AUTHORS OR COPYRIGHT HOLDERS BE LIABLE FOR ANY CLAIM, DAMAGES OR OTHER LIABILITY, WHETHER IN AN ACTION OF CONTRACT, TORT OR OTHERWISE, ARISING FROM, OUT OF OR IN CONNECTION WITH THE SOFTWARE OR THE USE OR OTHER DEALINGS IN THE SOFTWARE.

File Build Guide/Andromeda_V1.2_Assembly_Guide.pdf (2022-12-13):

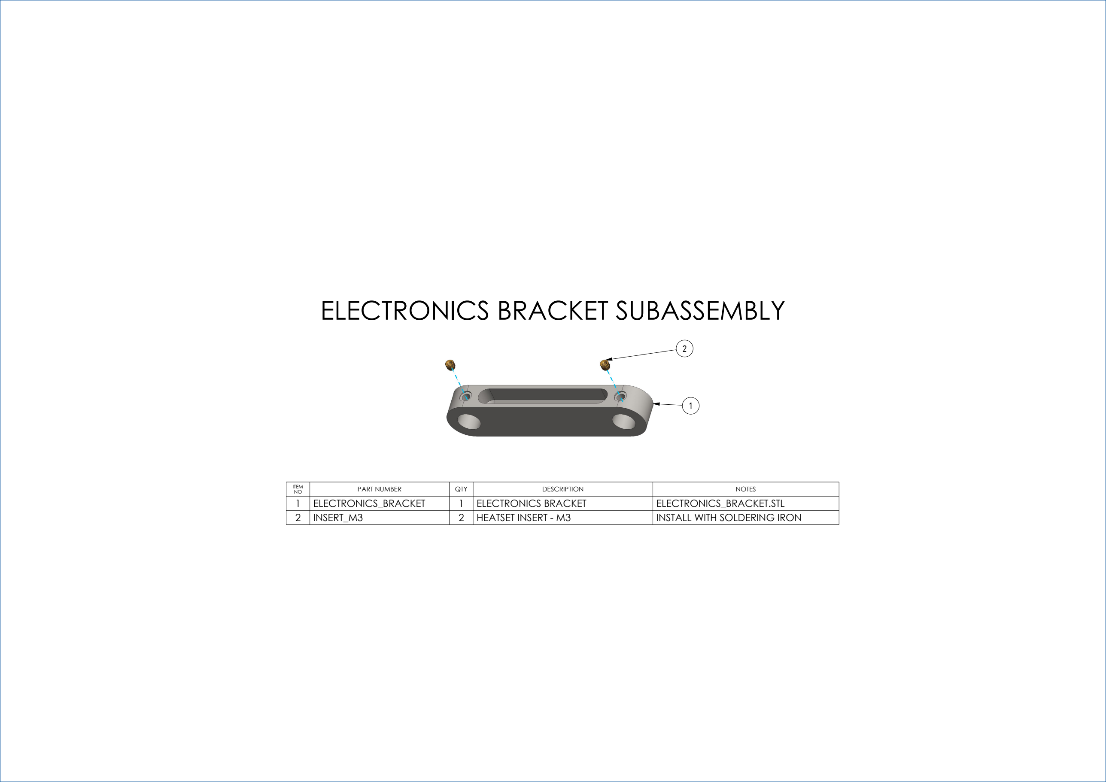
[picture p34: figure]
ITEM NO; PART NUMBER; QTY; DESCRIPTION; NOTES; ELECTRONICS_BRACKET; ELECTRONICS BRACKET; ELECTRONICS_BRACKET.STL; INSERT_M3; HEATSET INSERT - M3; INSTALL WITH SOLDERING IRON; ELECTRONICS BRACKET SUBASSEMBLY

ITEM NO | PART NUMBER | QTY | DESCRIPTION | NOTES
1 | FILAMENT_GUIDLER | 1 | FILAMENT GUIDLER | FILAMENT_GUIDLER.STL
2 | INSERT_M3 | 2 | HEATSET INSERT - M3 | INSTALL WITH SOLDERING IRON
3 | BEARING_623-2Z | 1 | BEARING 623-2Z | INSTALL AS SHOWN
4 | BHCS_M3_8MM | 1 | BUTTON HEAD CAP SCREW - M3 X 8mm | INSTALL AS SHOWN

# FILAMENT GUIDLER SUBASSEMBLY

3

4

1 | 2

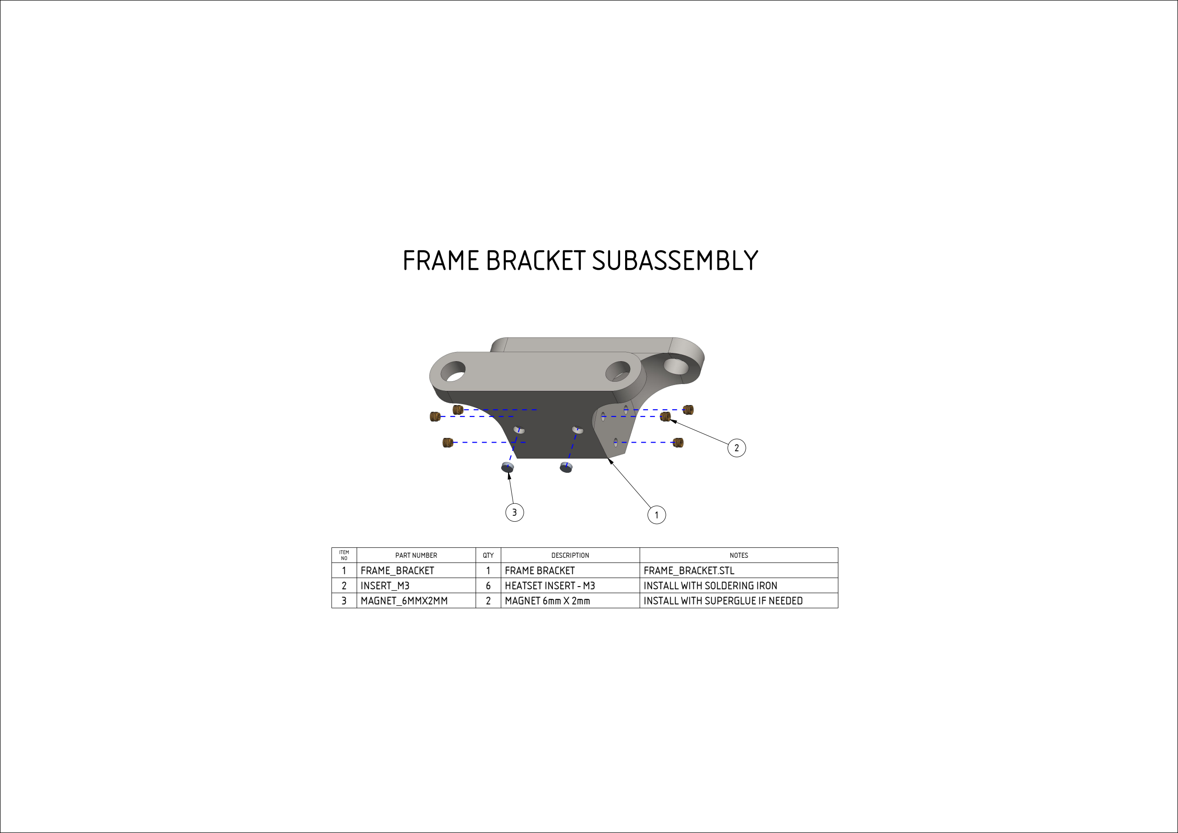
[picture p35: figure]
ITEM NO; PART NUMBER; QTY; DESCRIPTION; NOTES; FRAME_BRACKET; FRAME BRACKET; FRAME_BRACKET.STL; INSERT_M3; HEATSET INSERT - M3; INSTALL WITH SOLDERING IRON; MAGNET_6MMX2MM; MAGNET 6mm X 2mm; INSTALL WITH SUPERGLUE IF NEEDED; FRAME BRACKET SUBASSEMBLY

ITEM NO | PART NUMBER | QTY | DESCRIPTION | NOTES
1 | GEARBOX_OUTPUT_GEAR | 1 | GEARBOX OUTPUT GEAR | GEAR_BOX_OUTPUT_GEAR.STL
2 | BEARING_608-2RS | 1 | BEARING 608-2RS | PRESS INTO CENTER OF OUTPUT GEAR
3 | BHCS_M3_12MM | 8 | BUTTON HEAD CAP SCREW - M3 X 12mm | INSTALL AS SHOWN ABOVE
4 | INSERT_M3 | 4 | HEATSET INSERT - M3 | INSTALL WITH SOLDERING IRON
5 | NUT_M3 | 8 | HEX NUT - M3 | INSTALL AS SHOWN ABOVE

# GEARBOX OUTPUT GEAR SUBASSEMBLY

1 | 4 | 3 | 2 5

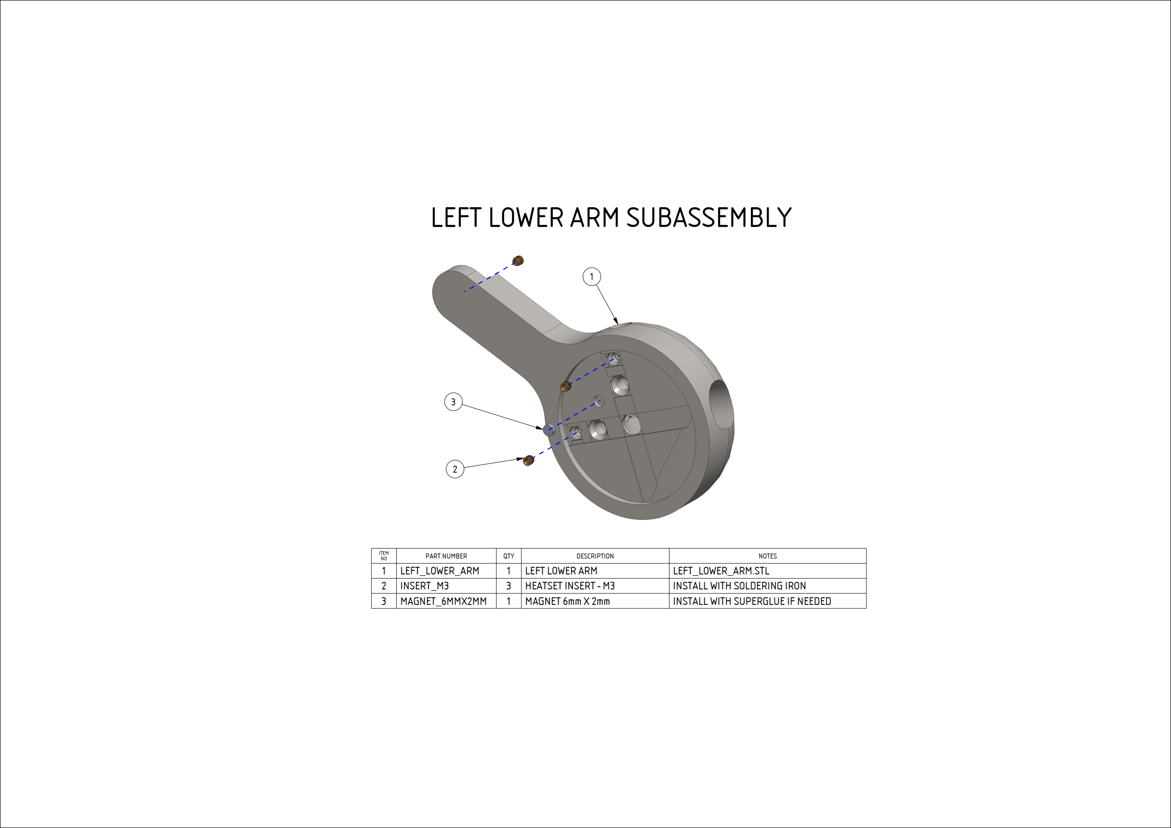
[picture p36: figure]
ITEM NO; PART NUMBER; QTY; DESCRIPTION; NOTES; LEFT_LOWER_ARM; LEFT LOWER ARM; LEFT_LOWER_ARM.STL; INSERT_M3; HEATSET INSERT - M3; INSTALL WITH SOLDERING IRON; MAGNET_6MMX2MM; MAGNET 6mm X 2mm; INSTALL WITH SUPERGLUE IF NEEDED; LEFT LOWER ARM SUBASSEMBLY

ITEM NO | PART NUMBER | QTY | DESCRIPTION | NOTES
1 | LEFT_UPPER_ARM | 1 | LEFT UPPER ARM | LEFT_UPPER_ARM.STL
2 | BHCS_M3_12MM | 1 | BUTTON HEAD CAP SCREW - M3 X 12mm | INSTALL AS SHOWN
3 | NUT_M3 | 1 | HEX NUT - M3 | INSTALL AS SHOWN

# LEFT UPPER ARM SUBASSEMBLY

1

3 | 2

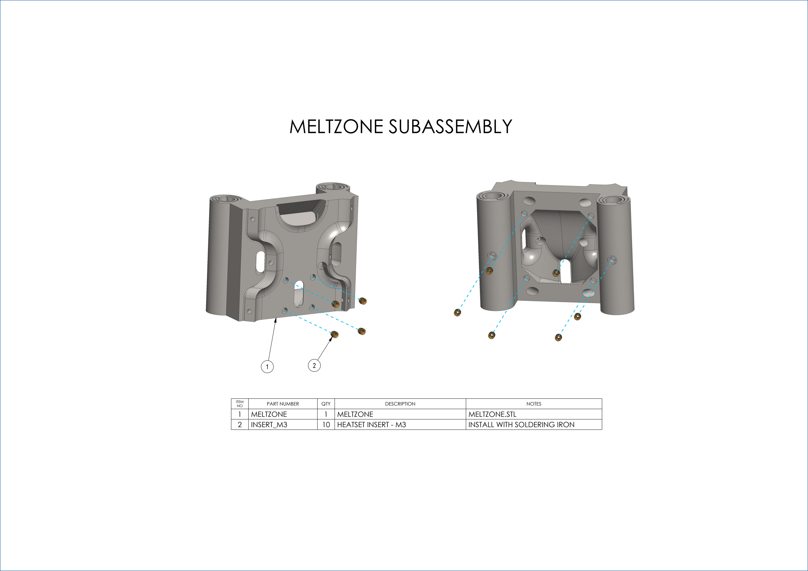
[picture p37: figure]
ITEM NO; PART NUMBER; QTY; DESCRIPTION; NOTES; MELTZONE; MELTZONE.STL; INSERT_M3; HEATSET INSERT - M3; INSTALL WITH SOLDERING IRON; MELTZONE SUBASSEMBLY

# MELTZONE COMPLETE ASSEMBLY

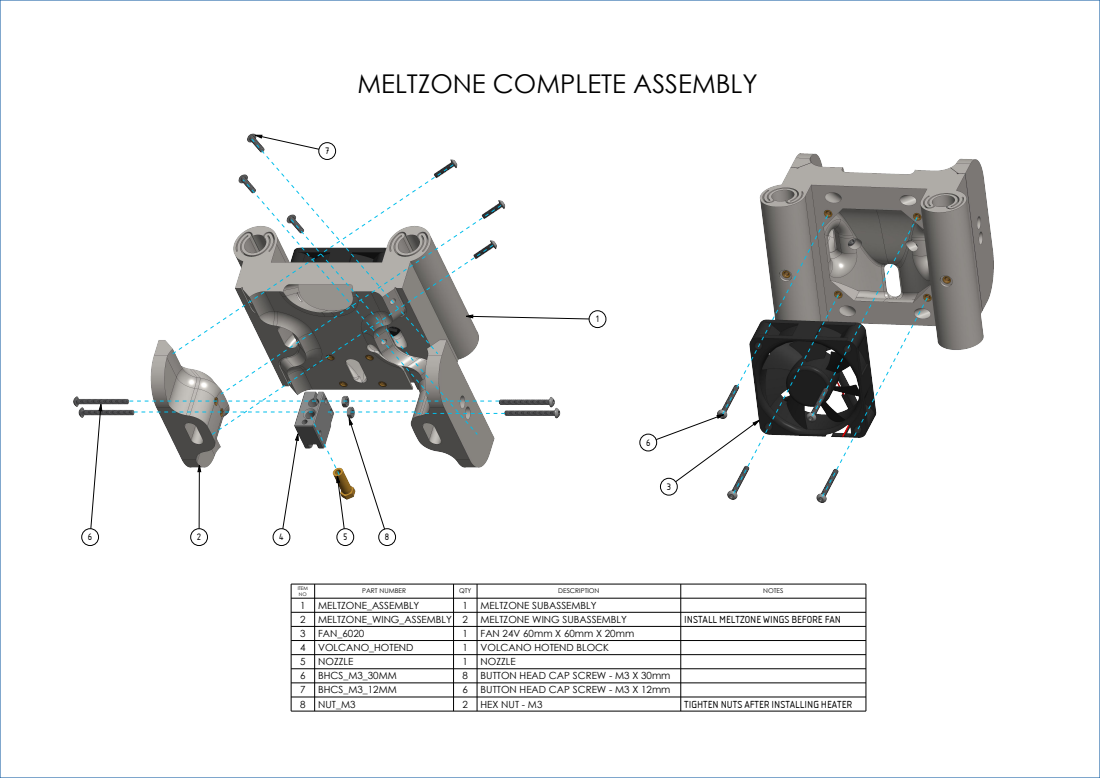
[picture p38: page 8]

ITEM NO | PART NUMBER | QTY | DESCRIPTION | NOTES
1 | MELTZONE_ASSEMBLY | 1 | MELTZONE SUBASSEMBLY
2 | MELTZONE_WING_ASSEMBLY | 2 | MELTZONE WING SUBASSEMBLY | INSTALL MELTZONE WINGS BEFORE FAN
3 | FAN_6020 | 1 | FAN 24V 60mm X 60mm X 20mm
4 | VOLCANO_HOTEND | 1 | VOLCANO HOTEND BLOCK
5 | NOZZLE | 1 | NOZZLE
6 | BHCS_M3_30MM | 8 | BUTTON HEAD CAP SCREW - M3 X 30mm
7 | BHCS_M3_12MM | 6 | BUTTON HEAD CAP SCREW - M3 X 12mm
8 | NUT_M3 | 2 | HEX NUT - M3 | TIGHTEN NUTS AFTER INSTALLING HEATER

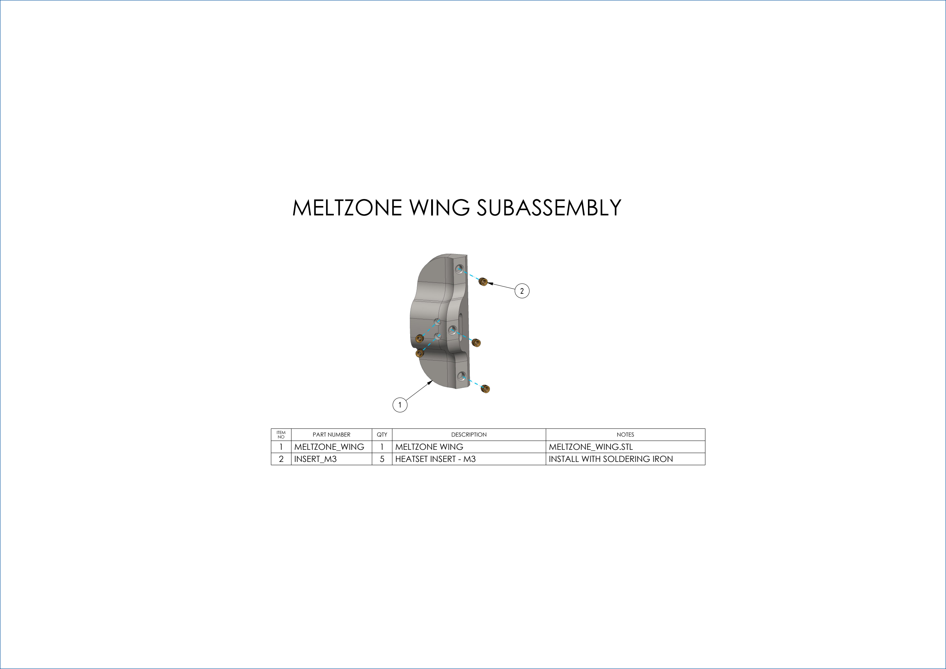
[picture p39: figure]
ITEM NO; PART NUMBER; QTY; DESCRIPTION; NOTES; MELTZONE_WING; MELTZONE WING; MELTZONE_WING.STL; INSERT_M3; HEATSET INSERT - M3; INSTALL WITH SOLDERING IRON; MELTZONE WING SUBASSEMBLY

ITEM NO | PART NUMBER | QTY | DESCRIPTION | NOTES
1 | OUTLET | 1 | OUTLET | OUTLET.STL
2 | INSERT_M3 | 4 | HEATSET INSERT - M3 | INSTALL WITH SOLDERING IRON
3 | BHCS_M3_6MM | 2 | BUTTON HEAD CAP SCREW - M3 X 6mm | INSTALL AS SHOWN
4 | C14_PANEL_MOUNT_PLUG | 1 | C14 PANEL MOUNT PLUG | INSTALL AS SHOWN

# OUTLET SUBASSEMBLY

1

2

3 4

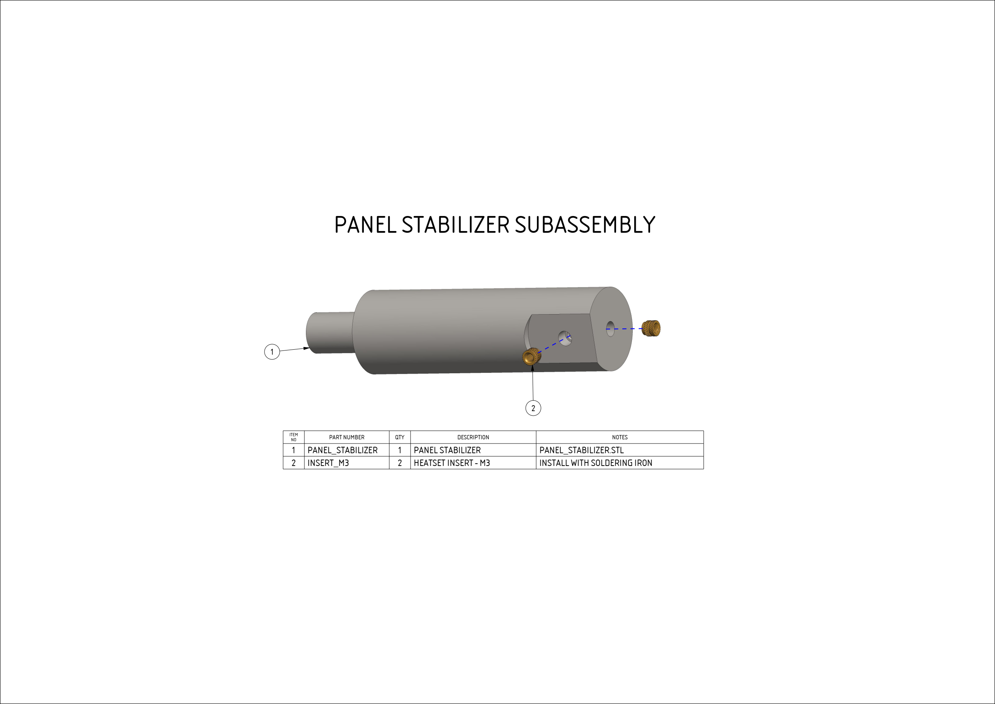
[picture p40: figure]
ITEM NO; PART NUMBER; QTY; DESCRIPTION; NOTES; PANEL_STABILIZER; PANEL STABILIZER; PANEL_STABILIZER.STL; INSERT_M3; HEATSET INSERT - M3; INSTALL WITH SOLDERING IRON; PANEL STABILIZER SUBASSEMBLY

Feel free to find these parts on Aliexpress too, they are mostly available on Triangle Labs and Mellow. And are usually much cheaper at the cost of taking longer to ship. The Amazon links are AFFILIATE links!!! It helps support the development and maintenance of the project. Component | BOM Qty Safe Qty | Notes | Link Hardware | M3x5x4mm Heatset Insert | check below | M3 x 5mm OD x 4mm Depth DFH Aliexpress Amazon Sparta3D(CA) Fermiolabs | $8
623 Bearings 3x10x4mm | 4 | Amazon (https://amzn.to/3yvEhWO) | $9
608 Bearing 8mm x 22mm x 7mm | 3 | Amazon (https://amzn.to/3O9GZXU) | $7
1/16in or 1.6mm drill bit | 1 | Amazon or Amazon
12mmx300mm Tubing or Rod (No wooden dowel please) (There is a shortage on the tube, please share the link in #resources if you find some) | 5 | Aliexpress or Amazon or Amazon or Amazon | $16 M3 (7mm*preferred - 6mm) x 0.5mm black oxide carbon steel washer | check below | DIN 125A | Amazon | $9 Assorted M3 BHCS screws 6/8/12/20/30mm | 1 | The link only has 50pcs 12mm, you need some more | Amazon | $16 M3 BHCS screws 12mm 100 Pack | 1 | The kit above doesn't have enough 12mm | Amazon Optional: Buy the screws separately | Boltdepot PTFE Lubricant | 1 | Amazon Optional: Wera 2mm Hex screwdriver 80mm length | 1 | Amazon or Amazon
Electronics | BTT SKR Pico, SKR 1.3 or any other cheaper MCU that can run Klipper | 1 | Amazon DFH | $55
6020 or 6025 24v Fan | 1 | Amazon DFH | $8 Raspberry Pi Zero W, or Raspberry Pi Zero 2 W, Raspberry Pi 1, Pi 2, Pi 3, Pi 4, (optional if you have a klipper printer) | 1 | RPI Tracker Micro SD Card (optional if you have a klipper printer) | 1 | Amazon NEMA17 stepper 59Ncm less than 48mm length | 1 | Amazon or Aliexpress | $14 C13 Power Cable | 1 | Amazon
C14 Panel Mount Plug | 1 | Amazon (https://www.amazon.com/FILSHU-Module-Switch-Connector-Holder/dp/B08PSS8B7K?s=industrial) | $9 Mean Well LRS-75-24 or LRS-100-24 power supply | 1 | Amazon or Amazon or Digikey or Digikey | $19 Option 1: Knock off Volcano+Thermistor+Nozzle Bundle (Good enough and cheap) | 1 | Amazon | $12 Option 1: 24v 40W heater cartridge (the bundle has a 64w cartridge which doesn't work, so please also get a 24v 40w cartridge) | 1 | DFH or Amazon or Microcenter Option 1: JST XH Extension cable | 3 | Amazon Option 2: E3D Volcano Heater Block | 1 | Amazon Option 2: 24v 40W Heater Cartridge | 1 | DFH or Amazon or Microcenter Option 2: M3 Screw Thermistor 104NT | 2 | Amazon Option 2: Genuine E3D Brass Volcano Nozzle - 3.00mm x 1.20mm / Generic 3.0mm x whatever nozzle | 1 | Amazon or Amazon Misc. | 6mmx3mm magnets | 24 | Amazon | $7

60C safety thermolabel (optional) 1 PaperThermometer Amazon E3D Volcano Hotend Silicon socks (optional, needs some cutting to fit) PLA, ABS, PETG or PET (Please adjust for the shrink rate in slicer, ex. ABS has ~0.6% sinkage, PETG has ~0.15%, or scale the model only in XY accordingly) 1 Printed Parts 1

2.0kg of main color and 0.5kg of accent color Fasteners list BHCS M3x6mm 39 ±10%

BHCS M3x8mm 14 ±10% BHCS M3x12mm 58 ±10% BHCS M3x20mm 9 ±10% Stainless Steel BHCS M3x30mm 13 4 ±10% M3 Nuts ±10% Carbon Steel M3 Washer 108 11 ±10% M3x5x4mm Heatset Insert ±10%

PolyCutter_Lite 623 Bearings 3x10x4mm 2 3 5 1 DFH Aliexpress Amazon Sparta3D(CA) Fermiolabs BHCS M3x12mm Aliexpress or Amazon or Amazon or Amazon Boltdepot 12mmx300mm Tubing or Rod (No wooden dowel please) (There is a shortage on the tube, please share the link in #resources if you find some) Amazon (https://amzn.to/3yvEhWO) Already included above M3x5x4mm Heatset Insert

Suppliers Fermiolabs-EU Decoprint3d-EU Kris3D_de-EU Vonwange-EU Lecktor-EU DFH(formossisima 3D printing)-US Fabreeko-US Printed_Solid-US Digmach-US kb3d-US Filastruder-US Sparta3D-CA 3dlabtech-CA Uniqueprints-AU Onetwo3D-GB printyplease-GB Powge-CN Magicstudios-CN

ITEM NO | PART NUMBER | QTY | DESCRIPTION | NOTES
1 | RIBBON_CARTRIDGE_HOLDER | 1 | RIBBON CARTRIDGE HOLDER | RIBBON_CARTRIDGE_HOLDER.STL
2 | INSERT_M3 | 2 | HEATSET INSERT - M3 | INSTALL WITH SOLDERING IRON
3 | MAGNET_6MMX3MM | 3 | MAGNET 6mm X 3mm | INSTALL WITH SUPERGLUE IF NEEDED

# RIBBON CARTRIDGE HOLDER SUBASSEMBLY

1
3 | 2

# RIGHT ARM DRIVE UNIT SUBASSEMBLY

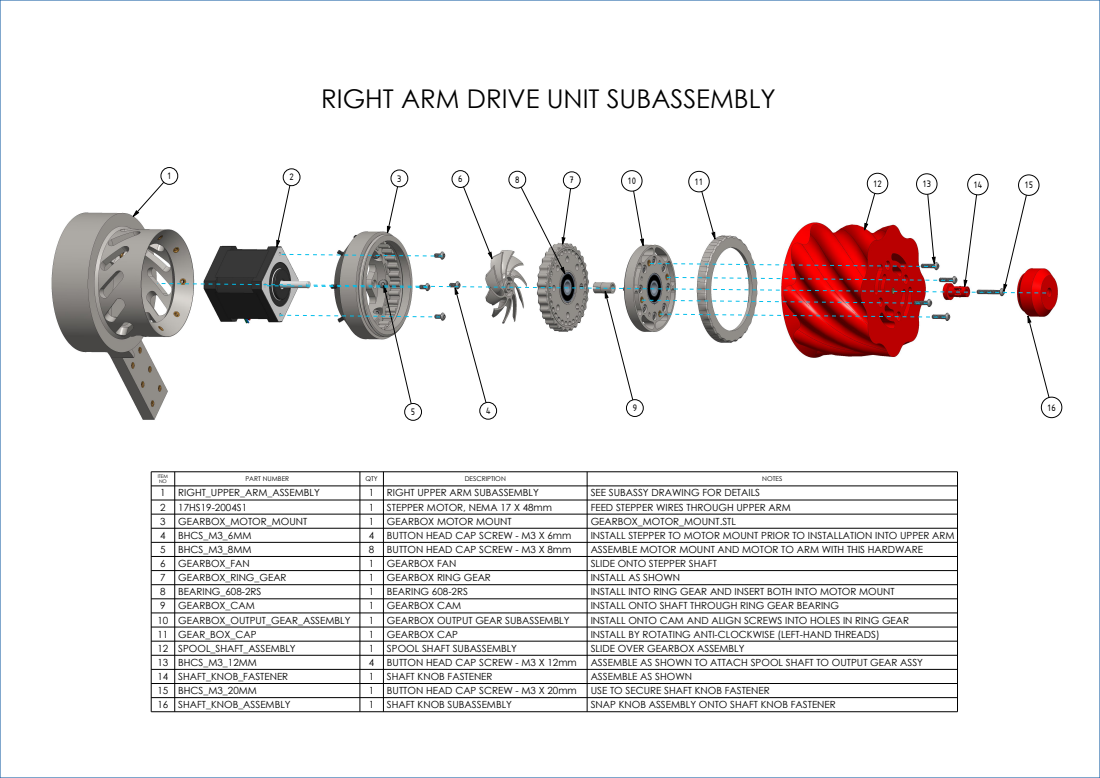
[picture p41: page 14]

ITEM NO | PART NUMBER | QTY | DESCRIPTION | NOTES
1 | RIGHT_UPPER_ARM_ASSEMBLY | 1 | RIGHT UPPER ARM SUBASSEMBLY | SEE SUBASSY DRAWING FOR DETAILS
2 | 17HS19-2004S1 | 1 | STEPPER MOTOR, NEMA 17 X 48mm | FEED STEPPER WIRES THROUGH UPPER ARM
3 | GEARBOX_MOTOR_MOUNT | 1 | GEARBOX MOTOR MOUNT | GEARBOX_MOTOR_MOUNT.STL
4 | BHCS_M3_6MM | 4 | BUTTON HEAD CAP SCREW - M3 X 6mm | INSTALL STEPPER TO MOTOR MOUNT PRIOR TO INSTALLATION INTO UPPER ARM
5 | BHCS_M3_8MM | 8 | BUTTON HEAD CAP SCREW - M3 X 8mm | ASSEMBLE MOTOR MOUNT AND MOTOR TO ARM WITH THIS HARDWARE
6 | GEARBOX_FAN | 1 | GEARBOX FAN | SLIDE ONTO STEPPER SHAFT
7 | GEARBOX_RING_GEAR | 1 | GEARBOX RING GEAR | INSTALL AS SHOWN
8 | BEARING_608-2RS | 1 | BEARING 608-2RS | INSTALL INTO RING GEAR AND INSERT BOTH INTO MOTOR MOUNT
9 | GEARBOX_CAM | 1 | GEARBOX CAM | INSTALL ONTO SHAFT THROUGH RING GEAR BEARING
10 | GEARBOX_OUTPUT_GEAR_ASSEMBLY | 1 | GEARBOX OUTPUT GEAR SUBASSEMBLY | INSTALL ONTO CAM AND ALIGN SCREWS INTO HOLES IN RING GEAR
11 | GEAR_BOX_CAP | 1 | GEARBOX CAP | INSTALL BY ROTATING ANTI-CLOCKWISE (LEFT-HAND THREADS)
12 | SPOOL_SHAFT_ASSEMBLY | 1 | SPOOL SHAFT SUBASSEMBLY | SLIDE OVER GEARBOX ASSEMBLY
13 | BHCS_M3_12MM | 4 | BUTTON HEAD CAP SCREW - M3 X 12mm | ASSEMBLE AS SHOWN TO ATTACH SPOOL SHAFT TO OUTPUT GEAR ASSY
14 | SHAFT_KNOB_FASTENER | 1 | SHAFT KNOB FASTENER | ASSEMBLE AS SHOWN
15 | BHCS_M3_20MM | 1 | BUTTON HEAD CAP SCREW - M3 X 20mm | USE TO SECURE SHAFT KNOB FASTENER
16 | SHAFT_KNOB_ASSEMBLY | 1 | SHAFT KNOB SUBASSEMBLY | SNAP KNOB ASSEMBLY ONTO SHAFT KNOB FASTENER

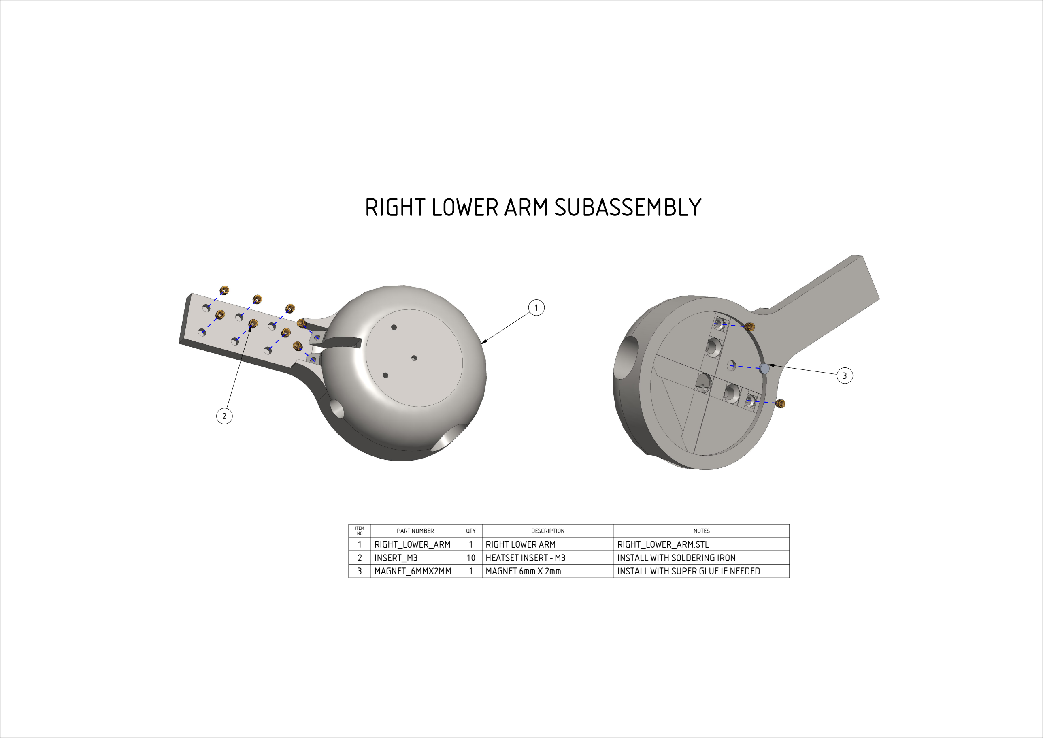
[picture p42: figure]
ITEM NO; PART NUMBER; QTY; DESCRIPTION; NOTES; RIGHT_LOWER_ARM; RIGHT LOWER ARM; RIGHT_LOWER_ARM.STL; INSERT_M3; HEATSET INSERT - M3; INSTALL WITH SOLDERING IRON; RIGHT LOWER ARM SUBASSEMBLY

3 | MAGNET_6MMX2MM | 1 | MAGNET 6mm X 2mm | INSTALL WITH SUPER GLUE IF NEEDED

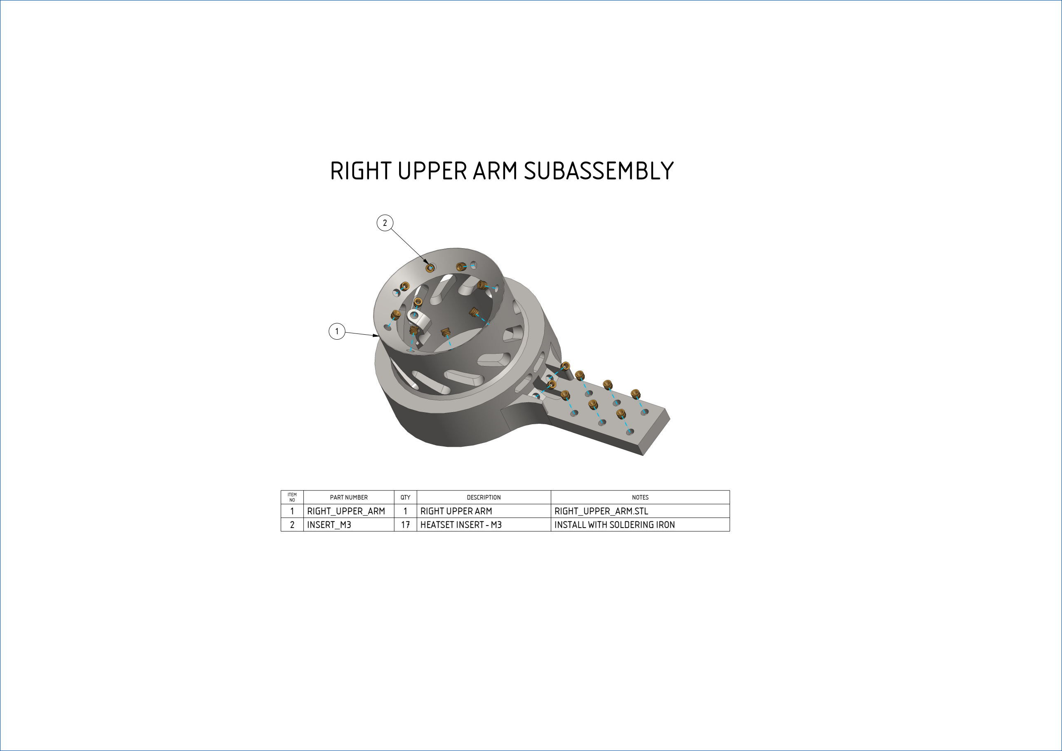
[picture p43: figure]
ITEM NO; PART NUMBER; QTY; DESCRIPTION; NOTES; RIGHT_UPPER_ARM; RIGHT UPPER ARM; RIGHT_UPPER_ARM.STL; INSERT_M3; HEATSET INSERT - M3; INSTALL WITH SOLDERING IRON; RIGHT UPPER ARM SUBASSEMBLY

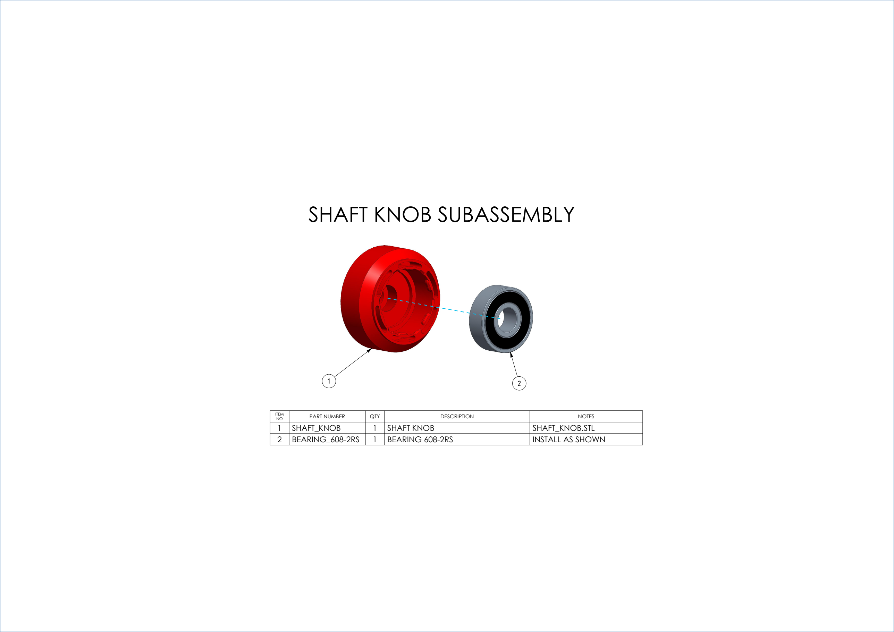
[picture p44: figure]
ITEM NO; PART NUMBER; QTY; DESCRIPTION; NOTES; SHAFT_KNOB; SHAFT KNOB; SHAFT_KNOB.STL; BEARING_608-2RS; BEARING 608-2RS; INSTALL AS SHOWN; SHAFT KNOB SUBASSEMBLY

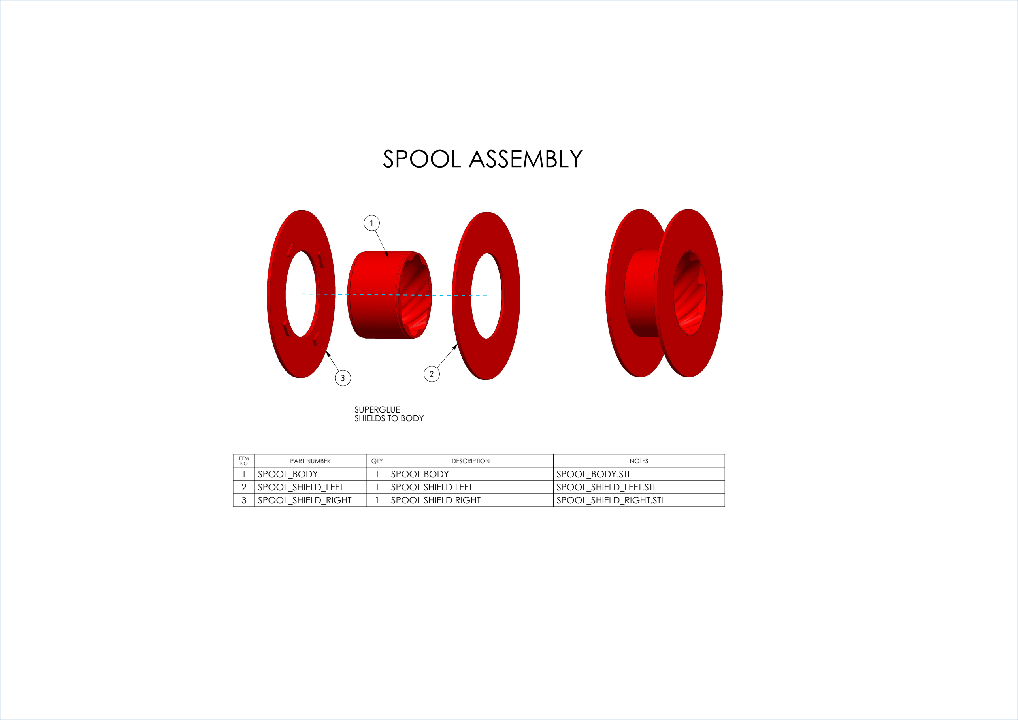
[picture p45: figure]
ITEM NO; PART NUMBER; QTY; DESCRIPTION; NOTES; SPOOL_BODY; SPOOL BODY; SPOOL_BODY.STL; SPOOL_SHIELD_LEFT; SPOOL SHIELD LEFT; SPOOL_SHIELD_LEFT.STL; SPOOL_SHIELD_RIGHT; SPOOL SHIELD RIGHT; SPOOL_SHIELD_RIGHT.STL; SPOOL ASSEMBLY; SUPERGLUE SHIELDS TO BODY

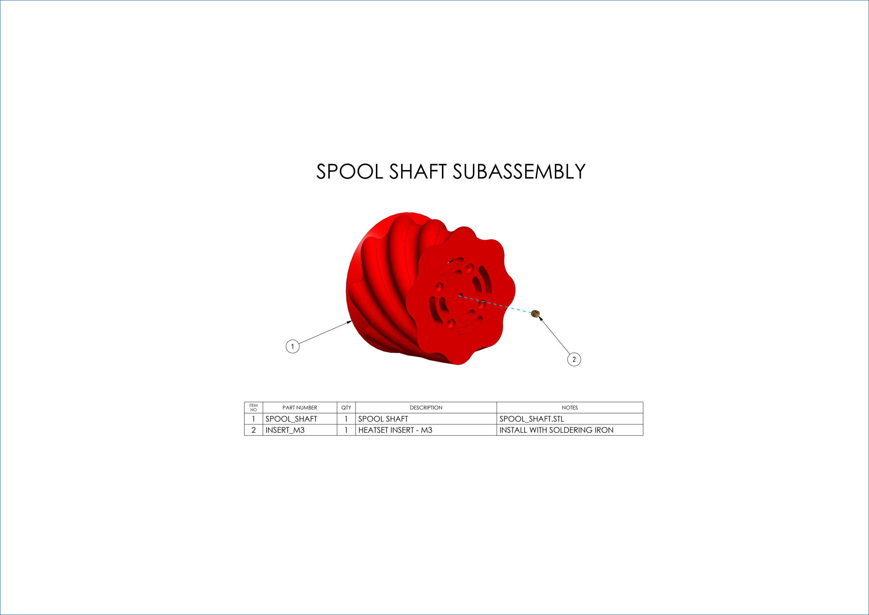
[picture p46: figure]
ITEM NO; PART NUMBER; QTY; DESCRIPTION; NOTES; SPOOL_SHAFT; SPOOL SHAFT; SPOOL_SHAFT.STL; INSERT_M3; HEATSET INSERT - M3; INSTALL WITH SOLDERING IRON; SPOOL SHAFT SUBASSEMBLY

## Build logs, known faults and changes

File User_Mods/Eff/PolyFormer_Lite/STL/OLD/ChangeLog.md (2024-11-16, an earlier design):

17/08/2023 - 

Ribbon Spool: Made sides smaller so could be printed without supports
Spool: Screw-in Spool, less screws required.

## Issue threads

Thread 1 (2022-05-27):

Where is the Build Guide?

chschmit, 2022-05-27:
Your website mentions a Build Guide on your GitHub, but I'm not finding it...only the CAD files.

FacuM, 2022-05-27:
I'm bumping that, where's that build guide? lol

milador, 2022-05-27:
Excellent work on the BOM file, software,  and CAD files! The guide is missing though as it's mentioned.

dbatey, 2022-05-27:
Looks like this one can be closed! Thanks for the crazy fast response :)

Reiten966, 2022-05-28:
build guide was in the discord and now I moved it here. I am working on a written guide as well but that is gonna take a while. A few assembly videos will do for now.

Closed 2022-05-28.

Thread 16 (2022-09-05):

Speed of filament production?

dhysuiej, 2022-09-05:
Could someone please point me where to find the info about how fast is the filament production? I'm estimating it could be somewhere around 60 mm/m (millimeters per minute).

Reiten966, 2022-09-06:
its about 15mm/s

dhysuiej, 2022-09-06:
Thanks. That's much faster than I was estimating (1 mm/s converted from 60 mm/m).

Closed 2022-09-06.

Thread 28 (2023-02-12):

Actual motor current is half of displayed motor current

Reiten966, 2023-02-12:
Currently, the default motor current is 700ma which is in fact 350ma at the system level. As we are working on solving this bug. Please set the current to 1400ma for the motor to function properly.

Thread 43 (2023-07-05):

Wiring the polyformer

schooltechnician, 2023-07-05:
Hello,

We've assembled the electronics according to the diagrams/instructions you have posted. However the screen on the machine won't turn on and the extruder heads are not heating up.
Would you be able post some more updated diagrams please regarding how the step motor is to be wired up to the circuit board? As the circuit board we obtained from your 'Ali Express' link appears to be different from the instructions.

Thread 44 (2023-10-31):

Settings to obtain a proper fillament

mejia921, 2023-10-31:
Hi everyone! I have been trying to obtain a good filament, but so far I can only roll the PET stripe without the usual structure, so the core of the filament is empty. Once I tried to use it in the printing machine, nothing could be printed, not even the base.

I'm wondering the best temperature for the set-up and rolling speed. Any advice?

Thanks

Reiten966, 2024-01-30:
Hi there, the core of the filament is supposed to be empty, it forms the strip into an "O" shape. You should print them at 270C and lower speed. Also reducing the tension on the extruder helps as it lowers the chance of the filament being crushed in the extruder.

zantiago261, 2024-08-07:
It doesn't work. At 240 degrees it doesn't melt plastic.

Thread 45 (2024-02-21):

Polyformer Kit

Omnianet, 2024-02-21:
Salve. Ho acquistato il Polyformer Kit. Da quello che ho capito la struttura della macchina va stampata in 3d, ma dove trovo i file del progetto da stampare?

zantiago261, 2024-07-08:
Hello. Where is the component Mean Well LRS-75-24? Does not include it.

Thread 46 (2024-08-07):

It doesn't work. At 240 degrees it doesn't melt plastic.

zantiago261, 2024-08-07:
he tratado de sacar filamento con las botellas pero no derrite el plástico. Los soportes para el extrusor no soportan las temperatura.

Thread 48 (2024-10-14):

Ribbon_Cartridge_Turning_Key

ozanolari, 2024-10-14:
Hello,
My classmates and I are working on assembling a Polyformer, but we are having trouble figuring out where to place the piece called [Accent Color] Ribbon_Cartridge_Turning_Key.stl.

We've watched the tutorial, but weren't able to understand where we should place it.
We would truly appreciate it if you could please let us know how you were able to install the piece.

Thank you.

ozanolari, 2024-10-18:
Hello,

I hope you are well. We are working on assembling the polyformer and were
wondering where you bought the nozzle/extruder and which type did you buy?

Thank you.

Regards,

Olivia

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

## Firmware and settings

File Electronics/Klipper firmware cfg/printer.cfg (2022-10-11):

# This file contains common pin mappings for the BIGTREETECH SKR Pico V1.0
# To use this config, the firmware should be compiled for the RP2040 with
# USB communication.

# The "make flash" command does not work on the SKR Pico V1.0. Instead,
# after running "make", copy the generated "out/klipper.uf2" file
# to the mass storage device in RP2040 boot mode

# See docs/Config_Reference.md for a description of parameters.

# Calibration:
#    - calibrate PID settings on extruder, open console and do:
#        - Set the part cooling fans to 25%: `M106 S64`
#        - run PID calibration: `PID_CALIBRATE HEATER=extruder TARGET=170`
#        - save the resilts in the `printer.cfg`file: `SAVE_CONFIG`
#
# References
#    - [TMC2209 Stepper driver](https://www.trinamic.com/fileadmin/assets/Products/ICs_Documents/TMC2209_Datasheet_V103.pdf)

# Adddtional configs
[include mainsail.cfg]
#[include macros.cfg]

[mcu]
serial:                # please follow the guide to get the serial ID
restart_method: command

# debugging: to manually verify stepper use [manual_stepper]
[extruder]
step_pin: gpio14
dir_pin: !gpio13
enable_pin: !gpio15
microsteps: 16            # TMC2209 driver supports: 8, 16, 32, or 64 microsteps (TODO: Add this to my config-and-calibration-README.md)
rotation_distance: 10.26
nozzle_diameter: 1.7
filament_diameter: 1.75
heater_pin: gpio23
sensor_type: Generic 3950       # look up your thermistor type
sensor_pin: gpio27
control = pid
pid_Kp: 22.2
pid_Ki: 1.08
pid_Kd: 114
min_temp: 0
max_temp: 300
min_extrude_temp: 0
max_extrude_cross_section:5
max_extrude_only_distance: 9999999

[tmc2209 extruder]
uart_pin: gpio9
tx_pin: gpio8
uart_address: 3
interpolate: false
run_current: 0.7        # look up the spec sheet for your stepper!!!	the current set here should =spec_current/1.414 *0.7
hold_current: 0.3
sense_resistor: 0.110
stealthchop_threshold: 0


# Triggered when the extruder is turned on
[heater_fan extruder_fan]
pin: gpio20
max_power: 1.0
shutdown_speed: 1.0
cycle_time: 0.01
kick_start_time: 0.5
heater: extruder
heater_temp: 50.0
fan_speed: 1.0

[temperature_sensor raspberry_pi]
sensor_type: temperature_host
min_temp: 10
max_temp: 100

[printer]
kinematics: none
max_velocity: 500
max_accel: 3000

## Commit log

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2022-05-03 Reinforced Arm, Redesigned cycloidal drive
    the old standalone cycloidal drive has been replaced with an integrated one. the 12:1 reduction ratio has been increased to 20:1 with the new design. BOM 54mm motor change to 60mm motor.
    [Filament_Guidler.stl, Filament_Guidler_Mirrored.stl, Frame_Bracket.stl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]
2022-05-03 Correct the length of the CAM
    [Gear_Box_CAM.stl]
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2022-05-04 Update Bottle Cutter, fixing assembly issues
    [Body.stl, Bottle_Cutter_5_4_2022.STEP, Bottle_Holder.stl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]
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2022-05-16 Update CAD, redesigned cyloidal drive
2022-05-19 Fix interference issue. Metal tubes should be able to easily slide in even after tightening the screws
    [Frame_Bracket.stl]
2022-05-21 optimizing printability for both left and right lower arms, print without supports
    [Left_Lower_Arm.stl, Left_Lower_Arm_Dont_Add_Supports.stl, Right_Lower_Arm.stl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]
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2022-05-25 folder name changed, bottle cutter should be printed with no supports
    [Body.stl, Bottle_Cap.STL, Bottle_Holder.stl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]
2022-05-25 meltzone print optimization, no need for additional supports
    [Meltzone_ABS_PETG_PET_PC_Nylon (Built-in Supports).stl, Meltzone_ABS_PETG_PET_PC_Nylon.stl]
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2022-05-27 fix ribbon holder missing feature
    [Ribbon_Holder.stl]
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2022-05-30 Updated STL Spreadsheet
    Updated the STL spreadsheet with compatible URL links to all STL's. The original formula only worked with Google Sheets
    [Polyformer Printed Parts Inventory _ checklist.xlsx]
2022-05-31 updating bottle cutter to use the same 12mm screw
    [Body.stl, Bottle_Cutter_5_31_2022.STEP, Bottle_Cutter_5_4_2022.STEP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]
2022-06-01 Adjust CAM tolerance
    [Gear_Box_CAM.stl]
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2022-06-08 Filament Guilder, Ribbon Holder major upgrades. Melt_Zone clears requirement for ABS or PETG, and small design change. Reduced built-in support material usage
    [Electronics_Bracket_4x.stl, Electronics_Bracket_4x_(no supports).stl, Filament_Guidler.stl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]
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2022-06-11 Small improvement to fit the steppers that have right angle connectors on them
    [Right_Upper_Arm.stl]
2022-06-12 Small update to eliminate the effect of elephant foot on the gearbox and add support for 695 bearings without flange
    [Gear_Box_CAM.stl, Gear_Box_Drive.stl, Gear_Box_Rotor.stl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]
2022-06-13 added metal washer for wear resistance on the slide gauge, got rid of the threaded inserts and increased the bearing overlap
    [Body.stl, Bottle_Holder.stl, Cutter.stl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]
2022-06-13 Add compliant fastening mechanism to filament guidlers and meltzone
    [Filament_Guidler_(need supports).stl, Filament_Guidler_Mirrored_(need supports).stl]
2022-06-14 more bearing overlap, detail refinement, and fastening the cutter with fasteners instead of glue
    [Body.stl, Bottle_Holder.stl, Cutter.stl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]
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2022-06-16 fix assembly issue, correct the hole size for inserts
    [Outlet.stl]
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2022-06-17 Added a 608 bearing based bottle cutter
    Added a 608 Bottle cutter variant with the option to use a 15m pipe
    [Body_608.stl, Bottle_Cap_608_15mmPipe.stl, Bottle_Holder_608.stl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]
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2022-06-18 small accuracies fix (-0.1mm)
    [Body.stl, Bottle_Holder.stl, Cutter.stl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]
2022-06-18 added a tiny chamfer, easier to install the screws for the bearings
    [Cutter.stl]
2022-06-18 Correct the 12mm hole tolerance
    [Electronics_Bracket_4x.stl]
2022-06-19 Adding a flange at the end to stop the spool from rubbing against the arm, increase assembly tolerance by 0.4mm, decrease chance of binding.
2022-06-20 changed the insert holes to be through hole, preventing plastic from backing into the inserts
    [Ribbon_Holder_Spindle_Core.stl]
2022-06-22 Add an alternative Frame Bracket
    Reduces the number of 12mm rods/tubes needed; replacing with an appropriate lengths of 2020 Aluminium extrusion
    [polyformer_2020_Bracket.scad, polyformer_2020_Bracket.stl]
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2022-06-23 Puller shaft and knob now uses screw connection instead of glue
    [[Accent Color] Spool_Shaft_Knob.stl]
2022-06-24 Added pocket for retention nuts
    Added pocket for retention nuts
    [Body_608.stl, Sliding_Gauge_608.stl]
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2022-07-06 bug fix
    [Right_Upper_Panel_Second_Half.stl]
2022-07-08 Mods by LHong820
    Includes right upper and lower arms with rod design and a mounting bracket for the BTT Pico
    [pico_bracket.stl, right_lower_arm_rod_design.stl, right_upper_arm_rod_design.stl]
2022-07-08 Updated to V1.3
    Thickened the body size, reinforced the cutter, increased bearing overlap, and added more throw to the Bottle holder
    [8mm Bottle Guide.stl, Bearing cutter v1.3.step, Body_608.stl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]
2022-07-14 small adjustment on tolerance
    [Ribbon_Cartridge_Holder.stl]
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2022-07-14 adjust tolerance
    [PolyPlane.STL]
2022-07-16 modified shaft_knob geometry to reduce strain on the wall, and also thickened the walls, reducing chance of breakage when inserting the bearings, Small adjustment on meltzone screw hole shoulders to 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
    [[Accent Color] Spool_Shaft_Knob.stl]
2022-07-17 tolerance adjustment
    [Filament_Mount_Spool_Side.stl]
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2022-07-18 adjusting tolerance
    [Ribbon_Cartridge_Cap_2x.stl]
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2022-07-22 Gearbox major Bug fix
    [Gear_Box_CAM.stl, Gear_Box_Cap.stl, Gear_Box_Output_Gear.stl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]
2022-07-25 strengthening the gears
    [Gear_Box_Output_Gear.stl]
2022-07-25 strengthen motor_mount
2022-07-25 ribbon_key accessibility fix
    [Ribbon_Cartridge_Holder.stl]
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2022-07-26 doc fixes and new docs
    added balloons to left lower arm
    add panel stabilizer
    add right upper arm
2022-07-27 fine tuning the tolerance on the gear, more printable
2022-07-28 Panel Locks increase in depth for the counterbores to accept 12mm screws better
    [Panel_Locks_x8.stl]
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2022-08-02 MeltZone geometry fixed, Gear Box fan now compliant
2022-08-04 reducing the play on the sliding gauge screws, adding rails to constrain the sliding gauge further.
    [Body.stl, Bottle_Holder.stl, Cutter.stl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]
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2022-08-30 -readjusting the gear_key tolerance, optimizing printability -using slicing wizardry to hide all the gear teeth, increase stiffness and make the key look super clean, -increase thickness from 9mm to 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
2022-08-31 -merging spool body with the right spool shield, saving one additional assembly process and make the spool stronger. decreasing spool material usage by hollowing out the center and adding ribs.
    [[Accent Color] Spool_Shield_Left.stl]
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2022-09-13 Update Sliding_Gauge.stl
    -loosening tolerance on the rail for the sliding gauge
    -adding fillets on sharp corners to prevent corner budging from binding the motion system
    [Sliding_Gauge.stl]
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2022-09-21 printability update
    change folder name, optimizing printability for ribbon cartridge holder and filament guide.
    [Electronics_Bracket_4x.stl, Filament_Guidler_(built_in_supports).stl, Filament_Guidler_(need supports).stl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]
2022-09-21 Update Ribbon_Cartridge_Holder_(built_in_supports).stl
    add a notch to prevent the cartridge from detaching
    [Ribbon_Cartridge_Holder_(built_in_supports).stl]
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2022-09-22 Body Update:
    - Merging the frame bracket with the left lower arm
    - lesser screws and no more support for the frame bracket
    - Adding cable management slot
    [Left_Lower_Arm_(Built-in Supports).stl]
2022-09-22 No longer needs frame bracket
    [Frame_Bracket_(Needs Supports).stl]
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2022-09-23 Panel update:
    - Adding tabs inside rail caps to help stop the shaft from interfering with the stainless tubes during installation.
    [Rail_Cap_Left.stl, Rail_Cap_Right.stl]
2022-09-23 Support free
    Panel Update:
    - Getting rid of the need for support, changing the unsupported perimeter on the gears to overhang perimeters.
    - rename all the folders to be support free
    [Body.stl, Bottle_Cap.STL, Bottle_Cap_Tensioner.STL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]
2022-09-23 Carriage Update:
    - Electronics bracket now gets rid of the super sharp overhangs on the edge.
    [Electronics_Bracket_4x.stl]
2022-09-25 Strengthen the arms
    [Right_Arm_Connector.stl, Right_Lower_Arm_(Built-in Supports).stl]
2022-09-27 adjusting clearance
    [Body.stl]
2022-09-28 avoid collision with bottles
    [Sliding_Gauge.stl]
2022-10-02 Carriage Update:
    - Ribbon_Cartridge_Turning_Key loosen tolerance on the sun gear, helps releasing.
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2022-10-11 strengthening polycutter
    [Body.stl, Cutter.stl]
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2022-10-13 Tighten tolerance and add built-in support for the body
    [Body.stl, Bottle_Holder.stl]
2022-10-14 Carriage Update
    -Ribbon cartridge thread tolerance rework
    -Ribbon cartridge reduce play
    [Ribbon_Cartridge_Cap_2x.stl, [Accent Color] Spool_Shield_Left.stl]
2022-10-16 adjust Cutter clearance and shrink the ribbon channel to better constrain the ribbon path
    [Cutter.stl]
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2022-10-23 Bottle Cutter Update:
    - Cutting core now features a constrained entry path, avoiding ribbon curling up prior to entry which has caused the bottle to bind up.
    - The end of the sliding gauge adjustment screw now goes inside the cutting core to be supported on two ends. Further reduing the play.
    - General reduction of the sliding gauge's play.
    [Body.stl, Bottle_Cap.STL, Bottle_Cap_Tensioner.STL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]
2022-10-31 fix sliding gauge slicing issue
    [Body.stl, Sliding_Gauge.stl]
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2022-11-07 Spool Update:
    Strengthening the filament mount
2022-11-07 increase screw tolerance
    [Electronics_Bracket_4x.stl]
2022-11-09 correct the quantity
    [Panel_Locks_x6.stl]
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2022-11-09 Updated firmware with bugfix for EBB42 v1.2 heater, and SH1106 screen variant
2022-11-11 Firmware Bugfix
    Corrected Radius size
    Stepper motor Sense resistor reconfigured to improve torque
    SH1106 Version added to remove 2 screen shift and noise on certain 1.3" displays
    Screen flip on SH1106 resolved
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2022-11-20 Gearbox update
    retune tolerance
    [Gear_Box_Output_Gear.stl]
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2022-11-23 reinforce the ring gear
2022-11-24 adjust tolerance and bottle holder tilt back
    [Body.stl]
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2023-01-07 Gearbox Update: -Redesign the bearing slot geometry on the ringgear and output gear, hopefully to solve some of the longevity issues with the bearing slot as there are reports of bearing getting loos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
    [Gear_Box_Output_Gear.stl]
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2023-01-17 update tolerance, resolve fitting issue
    [Ribbon_Cartridge_Cap_2x.stl]
2023-01-25 readjust tolerance
    [Gear_Box_CAM.stl, Gear_Box_Output_Gear.stl]
2023-02-19 A mount for DFH kit display
    A mount for DFH kit display to use with a no panels PF. labtopia#7948
    [LABTOPIAS_IMPERFECT_DFHKIT_DISPLAY_MOUNT.stl]
2023-02-20 Added a display mount for no-panels PF
    This is a mount for DFH kit display to be used on PF without panels. It sticks into the existing frame holes on the extruder end.
    [LABTOPIAS_IMPERFECT_DFHKIT_DISPLAY_MOUNT.stl]
2023-03-16 Add files via upload
    Uploaded a Screen Stand to be used without the panels on the Polyformer. Two of these are to be printed then affixed to the existing Polyofmrer Screen.
    [Screen Mount Stand (Works with Existing Screen Mount).stl]
2023-03-16 Add files via upload
    Uploaded an STL to allow the existing Screen Mount to be connected to the Polyformer. Print two of these and attach to Screen Mount using a couple of screws then slide into the holes at the front of 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
    [Screen Mount Stand (Works with Existing Screen Mount).stl]
2023-04-03 Split Ring Planetary Gearbox
    Added STL files for the 70:1 split ring planetary gearbox
    [Housing.stl, Input Sun 16T.stl, Output Gear 42T.stl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]
2023-04-03 Fix output gears and print orientation
    Reversed the helix direction on the output gears to match what they should be. Updated the STL files to be oriented the same as they should print.
    [Housing.stl, Input Sun 16T.stl, Output Gear 42T.stl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]
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2023-04-07 Update Input Sun 16T.stl
    Input sun with more clearance for motor shaft
    [Input Sun 16T.stl]
2023-04-07 Reoriented new/updated parts
    Laid the updated input gear and fan down so that they are in the orientation they should be printed in.
    [Input Sun 16T.stl]
2023-05-10 Clarified planet gear orientation
    Added a square to the previously blank planet gear and noted the correct orientation in the readme
    [Planet Gear 1.stl]
2023-05-14 Split ring gearbox now official
    replaced original cycloid gearbox with the split ring one
    [Gear_Box_CAM.stl, Gear_Box_Output_Gear.stl, Housing.stl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]
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
